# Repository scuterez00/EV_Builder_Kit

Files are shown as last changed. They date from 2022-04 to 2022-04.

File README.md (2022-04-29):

# EV_Builder_Kit Engineering Addendum
Erbyn Bonilla, Henry Chong, Stephanie Cuterez, Linglong Le, Michelle Imogu

EC464 - Spring 2022

## Summary and Project Motivation
As countries and institutions start pushing to replace fossil fuel driven vehicles with zero emission vehicles such as electric cars, there will inevitably be skepticism and doubt expressed towards this change. These doubts have a variety of sources, whether it be a lack of familiarity with how electric vehicles work, or a belief that electric vehicles cannot operate as well as gas powered vehicles. To combat these sources of doubt, this project will create a small-scale model of a transportation grid completely powered by electric vehicles. There will be multiple small vehicles that users can drive around and link with provided charging stations for recharging. These vehicles will transmit mileage and battery charge remaining in the model car to the users. A set of controllers will also be provided for user interaction with the model, allowing people to come up and drive the vehicles around.  Charging stations utilizing a variety of methods, ranging from solar panels to outlet power, will be provided for recharging the vehicles. And everything will be integrated into a set of roads and decorations to create a semi-realistic transportation system. This will create an electric vehicle kit that will show the operation cycle of electric vehicles. In the process of using the kit, users will be provided with a clear demonstration of the process of charging, driving, and recharging the vehicles. 

## Main Features of this Repository
As of now, the repository contains all the schematics needed for the replication of the casing and circuitry of two items: the electric vehicles and the controllers for these electric vehicles. Associated datasheets and schematics for this portion of the project can be accessed using [README_HARDWARE.md](README_HARDWARE.md). Additionally, this repository also contains the code that must be uploaded to the microcontrollers on the cars and controllers for the communications between the two to begin. For a brief summary of the code please view [README_SOFTWARE.md](README_SOFTWARE.md).

## Current State of the Project
### Cars
The information in this repo corresponds to a set of working electric vehicles that can drive forwards, backwards, and turn in response to a users inputs on an associated controller. The car is capable of sending relevant battery data to the controller via the transceiver, and displays the current state of control using LEDs. When the power is switched off the car is still capable of charging via a DC jack connected to either a solar panel or a DC adapter, or a USB-C cable.

The method the cars use to drive around is via differential drive, meaning that the two back wheels can rotate independently of each other, while the front wheels are left to be free spinning. This was done to reduce the amount of motor drivers required as compared to four wheel drive, and reduce the complexity of the mechanical system required to create front wheels for facilitating turning.

One thing to note is that no PCB was utilized for any of the electronics, and as a result there are no PCB files available for creating the circuitry outlined in the hardware report. Similarly no CAD was utilized for the creation of the car bodies, so no files are available for quickly reproducing the bodies via machining.

### Controllers
The information in this repo corresponds to a working controller that can communicate with the cars, and display relevant details about the car onto the attached LCD. Using the joysticks, the user will be able to control the vehicle, while the toggle switches are used to switch which vehicle is being controlled. The controller provided here uses 3 switches to toggle between 3 possible cars for control. The controller is powered using 4 AA batteries, and as a result requires new batteries to be provided upon running out of charge.

The current set-up of the controller is so that the left joystick is pushed vertically to control the car's forward/reverse motion, while the right joystick is pushed horizontally to cause the car to turn. To know which car the controller is controlling, flip the switches to toggle between vehicles, and look for the vehicle with a lit up LED. The LED corresponds to having an open reading pipeline to receive controller data.

### Track and Surrounding Model
Tracks and auxiliary models such as grass, trees and buildings were also used in the project, but have not been included in this repository. This is because the models were purchased and not designed, thus their CAD files and designs cannot be placed into this repository. As for the track, this track simply consists of adhesive black tape laid out onto flat boards to denote roadway, and as a result not included in this repository either.

## Things to look out for
- Depending on the type of microcontroller you are using, specific drivers will be required. In our case we were not using official Arduino Nano microcontrollers for our project, thus we had to use the CH340 drivers. If you are using official microcontrollers these drivers will not be needed.
- The nRF24L01 transceivers have only a single pipeline for communication, which means that they cannot transmit and receive at the same time. To circumvent this our code uses cycles to switch between transmission and reception mode on the transceivers of the controllers and the cars. The controller's transceiver first sends out a specific message while swapping to receiving. This message will cause the transceiver on the car to close the pipeline, and then switch from receiving to transmitting, before transmitting a message. Once the controller transceiver receives this message, they send out another signal which will return the controller's transceiver to transmission mode and the car's transceiver to reception mode.
- Due to the use of differential drive, the center of gravity of the the vehicle, along with the traction of the wheels are critical for the cars to handle properly. This means that the center of gravity should be shifted towards the central axis of the differnetial drive.

## Known Bugs
- Occasionally the cars will become completely unresponsive to the controller, and switching the power button will not be able to solve this. To fix this issue unplug the battery from the car, then flip the power switch 5 times. After this you can replug the battery and the system should work again.

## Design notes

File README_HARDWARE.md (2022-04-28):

# Hardware Report
This is a report which covers the fundamentals of the hardware, including both the circuitry and the casing/bodies made to house the products.

## Cars
This section will deal with the circuitry and casing for the electric cars.

### Car Bodies
**Car Front:**
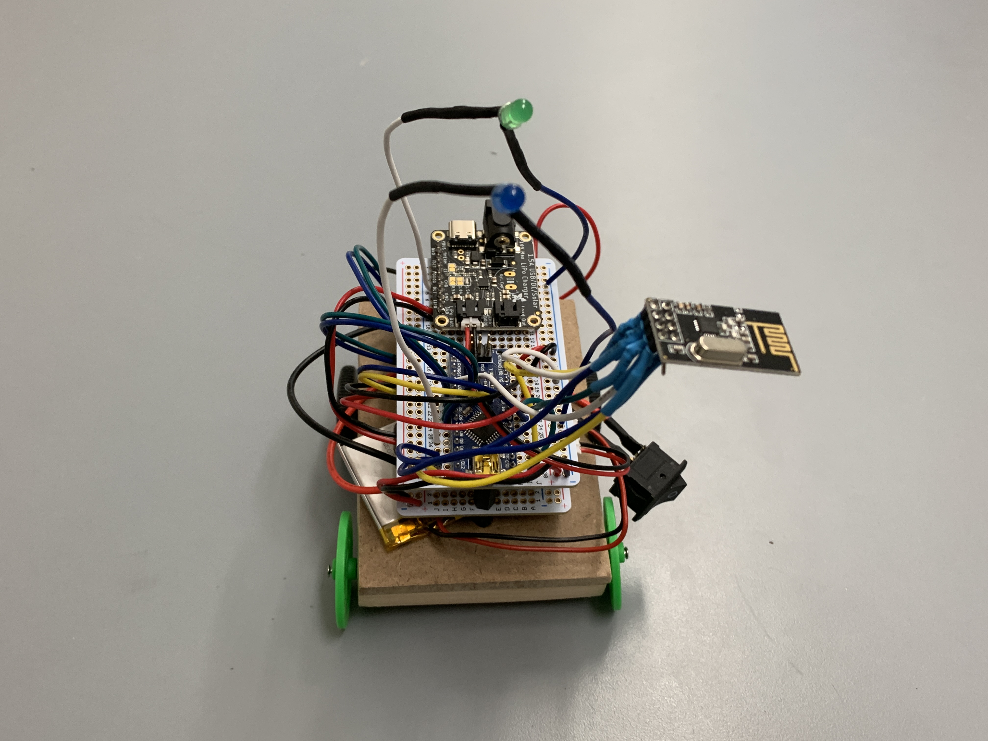
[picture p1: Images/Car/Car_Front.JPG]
Car Front


**Car Side:**
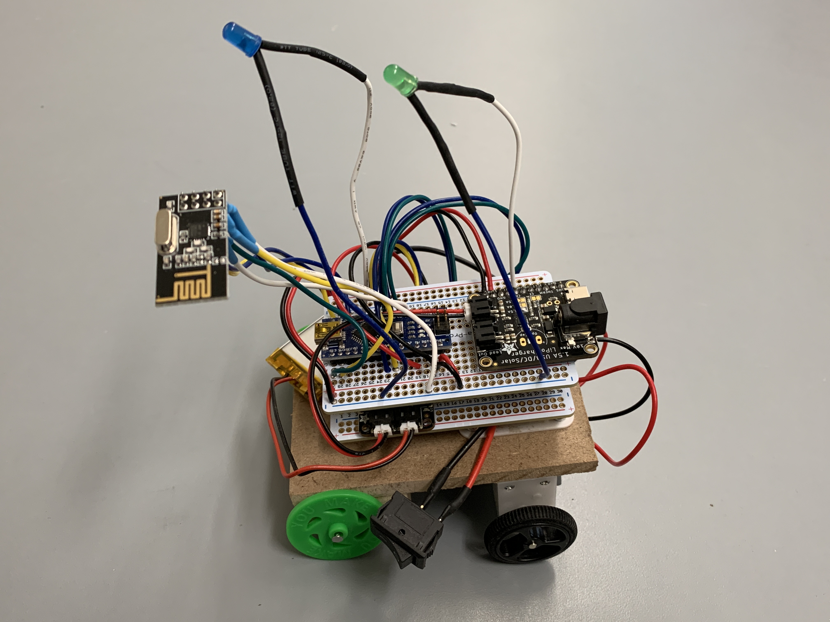
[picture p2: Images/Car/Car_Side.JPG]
Car Side


**Car Back:**
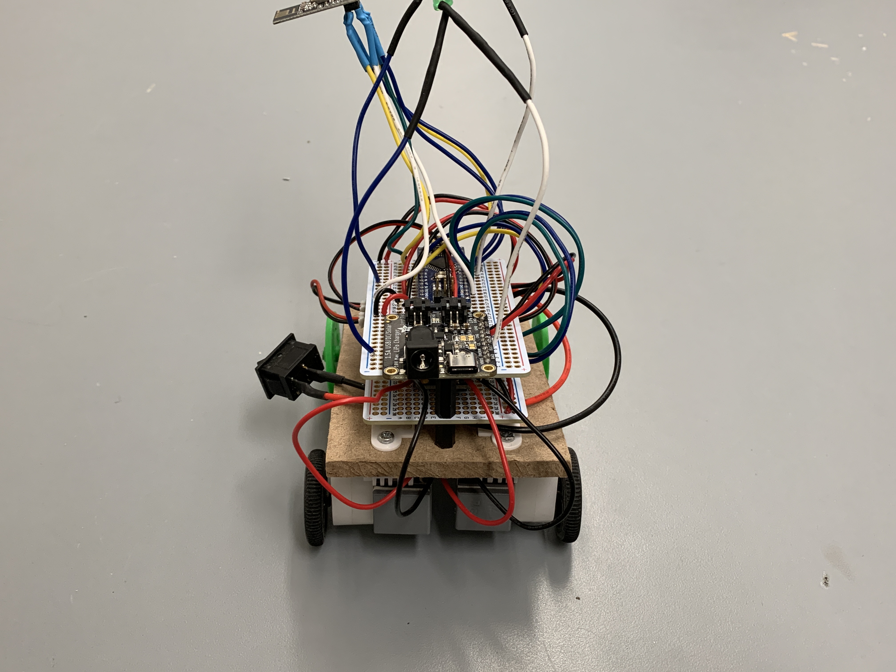
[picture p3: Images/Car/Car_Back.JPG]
Car Back


**Car Bottom:**
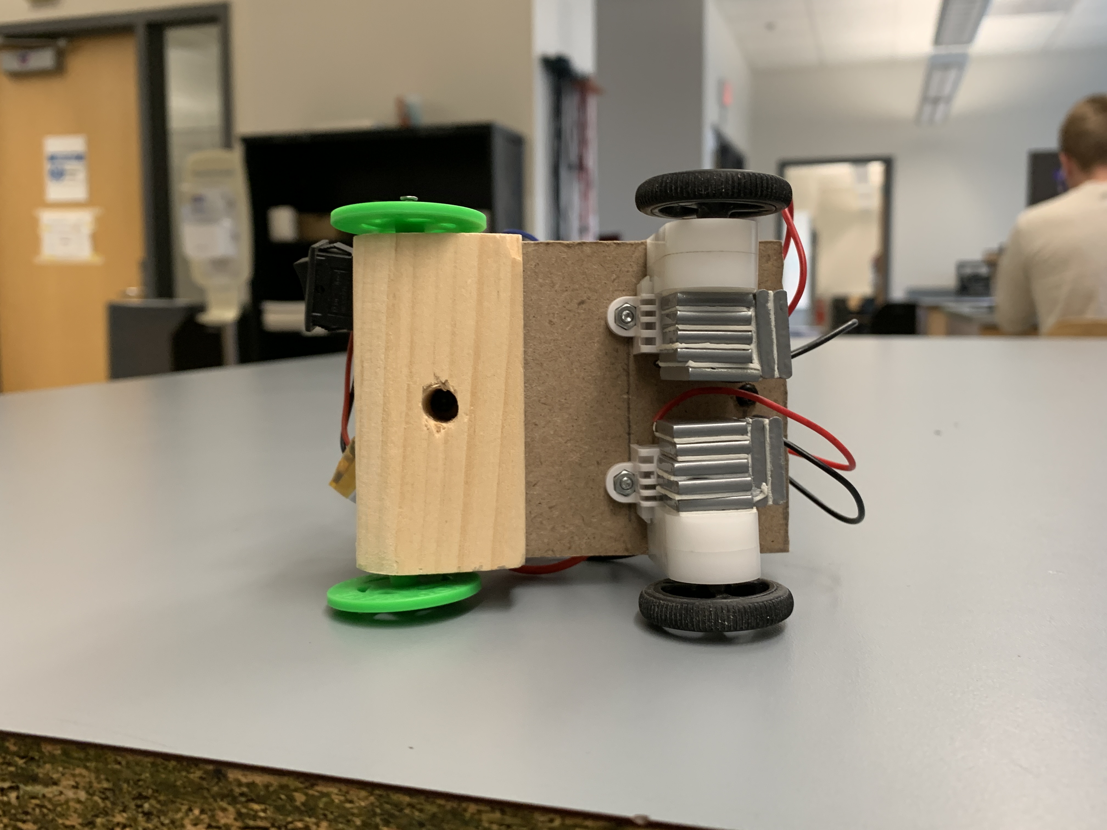
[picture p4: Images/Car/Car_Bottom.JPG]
Car Bottom

  Shown here are 4 views of one of the fully assembled cars. The car in question here is a Light Duty Vehicle(LDV) Equivalent. The car body was made using 1/8" thick Medium-Density Fiberboard(MDF) and 2" by 1" wood planks. The MDF board is used to house the circuit tower and mount the motors and weight, while the wood plank is used to hold the front wheels in place, using nails. Holes were drilled into the MDF board for the purpose of screwing in the circuitry components. A large hole was drilled into the bottom of the 2" by 1" plank so that screws could be attached to hold the entire circuit tower in place.

### Car Circuitry
**Circuit Tower Bottom:**
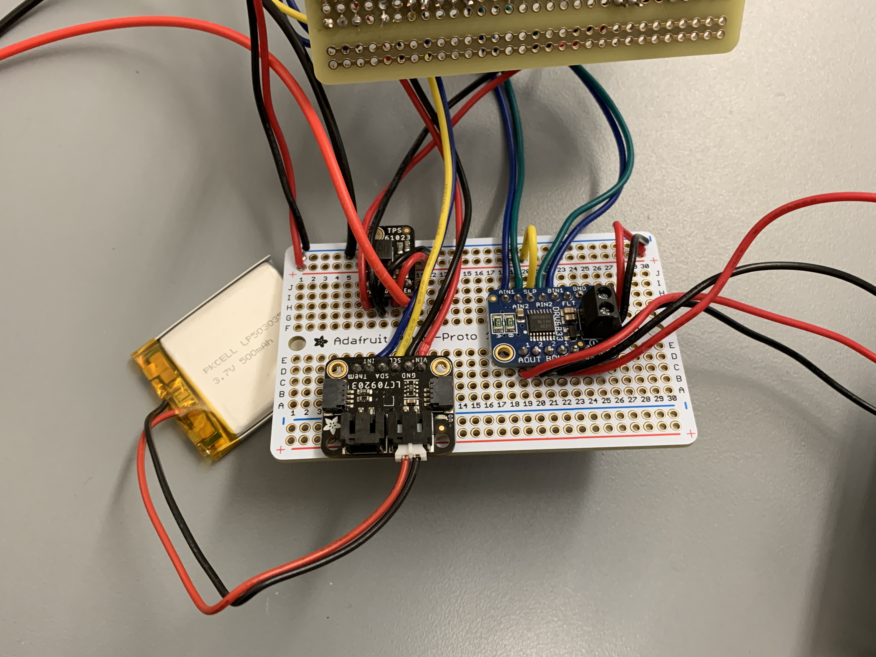
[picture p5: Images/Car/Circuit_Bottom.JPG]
Circuit Tower Bottom

  The circuitry from the car is soldered onto two breadboards, and mounted one on top of the other using PCB screws. The picture above shows three major components: the motor driver, the battery monitoring chip, and the voltage regulator. The motor driver is responsible for controlling motor speed and direction, while the battery monitoring chip provides data on the battery charge and state. The voltage regulator is used to convert the 3.7 Volts from the lithium polymer(LiPo) battery to 5 Volts for the rest of the system. One thing to note is that the on-off switch attached to the vehicle is linked to the Enable(EN) pin of the voltage regulator. When the switch is turned off the EN pin is pulled to ground, disabling the 5 Volt output powering the car circuitry, while keeping the battery connected to the charging circuit.

**Circuit Tower Top:**
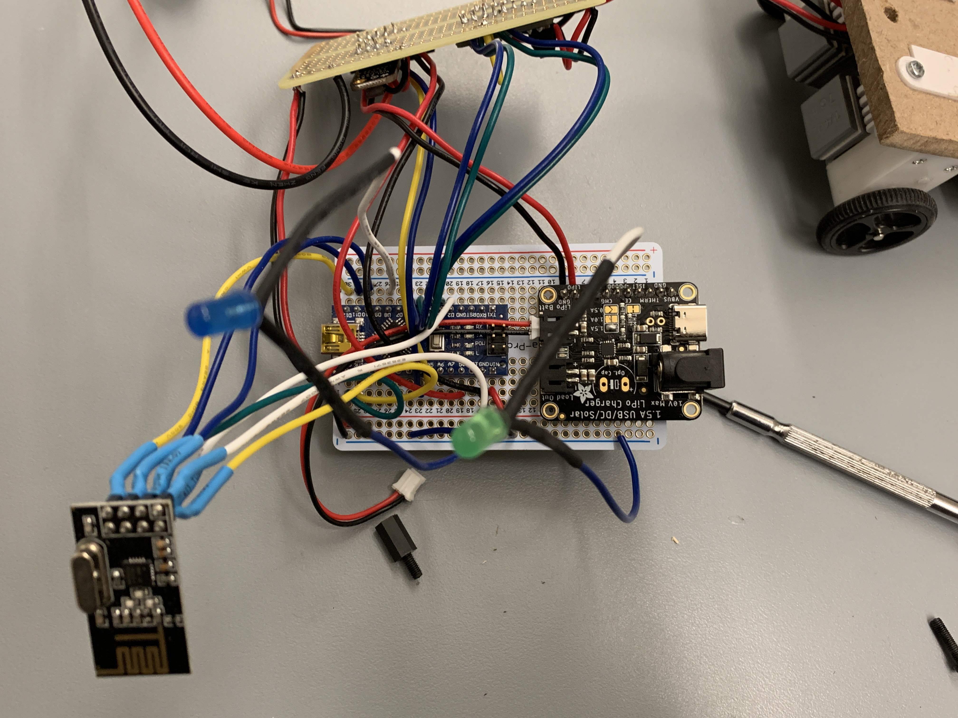
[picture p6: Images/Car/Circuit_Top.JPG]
Circuit Tower Top

  Shown here is the top of the circuitry tower, which contains the following: the NRF24L01 transceiver chip, the microcontroller (an Elegoo Nano), and the LiPo Charging chip. The transceiver is responsible for communication between the car and the controllers, while the microcontroller is responsible for performing all the computations and translations necessary to control each component of the car. The LiPo Charging chip is attached to provide a regulated method of charging the LiPo battery, utilizing either a 3.5 mm DC jack, or a USB type C Cable. Also shown here are LEDs attached to provide the user feedback on control and charging.

### Car Circuit Schematic

[Link to PDF](/Circuit_Schematics/Car_Circuit_Abstraction.pdf)

[Link to PDF](/Circuit_Schematics/Car_Circuit.pdf)
 
Shown here is a circuit diagram and an associated abstraction. Essentially the circuit can be split up into two different components, the battery circuit and the operational circuit. The operational circuit operates on 5 volts and consists of: the microcontroller, voltage regulator, motor driver, motors, and transceiver. This circuit is what drives radio communication and driving of the car. The battery circuit on the other hand consists of the LiPo Fuel Gauge and the LiPo Charging Chip, and serves to monitor and recharge the battery. The output of the battery circuit is fed to the voltage regulator to actually power the rest of the operational circuit. Thus by turning off the voltage regulator using a switch, we are able to maintain the ability to charge the battery while cutting power off from the car.

### Car Body Schematic

[Link to PDF](/Hardware_Schematics/Car_Schematic.pdf)

Shown here is the drawing used to create the body of the cars. This is the drawing for the LDV variant of the cars. The body is made up of two main components: the 1/8" thick MDF board and the 2" by 1" wood plank. The MDF board is drilled so that all the circuit components can be attached using screws, while the plank is super glued to the front of the MDF board, for mounting the wheels. Once all the circuitry has been attached and screwed in, steel weights are then added to the back of the vehicle, to improve the vehicle's handling by shifting the center of gravity towards the motored wheels. No CAD files were created as all components were made by hand.

### Bill of Materials
#### Light Duty Vehicle(LDV) variant Car

This bill of materials covers the material needed to create one LDV car, and does not include components such as nails, screws and wires.

| Item | Amount | Vendor | Datasheet Link |
| --- | :---: | :---: |:---: |
| Microcontroller | 1 | Amazon | [Link](/Data_Sheets/Nano_Pinouts.pdf)|
| Transciever | 1 | Amazon | [Link](/Data_Sheets/nRF24L01_Datasheet.pdf)|
| Battery Monitoring Chip| 1 | Adafruit  | [Link](/Data_Sheets/Battery_Monitor_Datasheet.pdf)|
| Battery Charging Chip | 1 | Adafruit | [Link](/Data_Sheets/Charger_Datasheet.pdf)|
| Battery | 1 | Adafruit |  [Link](/Data_Sheets/Battery_Datasheet.pdf)|
| Voltage Regulator| 1 | Pololu |  [Link](/Data_Sheets/Pololu_Regulator_Sheets/Chip_Datasheet.pdf)| 
| Motor Controller | 1 | Adafruit | [Link](/Data_Sheets/Motor_Driver_Datasheet.pdf)| 
| Plastic Motor | 2 | Pololu | [Link](/Data_Sheets/Plastic_Motor_Specifications.pdf)|  
| Motor Wheels | 2| Pololu | [Link](/Data_Sheets/Dimensions/Pololu_Wheel_Dimensions.pdf)|
| Plastic Motor Brackets | 2 | Pololu | [Link](/Data_Sheets/Dimensions/Plastic_Motor_Mounts_Dimensions.pdf) |
| Front Wheels | 2 | Amazon | [Link](https://www.amazon.com/gp/product/B073W18BP3) |
| Steel Weights | 10 | Amazon | [Link](https://www.amazon.com/gp/product/B06XDHXRT7)|
| Solderable Breadboard | 2 | Adafruit | [Link](https://www.adafruit.com/product/1609)|
| LEDs | 2 | Amazon | N/A |
| 1/8" MDF Board| 1 | Home Depot | N/A |
| 2" by 1" Plank | 1 | Home Depot | N/A |

#### Heavy Duty Vehicle(HDV) variant Car

This bill of materials covers the material needed to create one HDV car, and does not include components such as nails, screws and wires.

| Item | Amount | Vendor | Datasheet Link |
| --- | :---: | :---: |:---: |
| Microcontroller | 1 | Amazon | [Link](/Data_Sheets/Nano_Pinouts.pdf)|
| Transciever | 1 | Amazon | [Link](/Data_Sheets/nRF24L01_Datasheet.pdf)|
| Battery Monitoring Chip| 1 | Adafruit  | [Link](/Data_Sheets/Battery_Monitor_Datasheet.pdf)|
| Battery Charging Chip | 1 | Adafruit | [Link](/Data_Sheets/Charger_Datasheet.pdf)|
| Battery | 1 | Adafruit |  [Link](/Data_Sheets/Battery_Datasheet.pdf)|
| Voltage Regulator| 1 | Pololu |  [Link](/Data_Sheets/Pololu_Regulator_Sheets/Chip_Datasheet.pdf)| 
| Motor Controller | 1 | Adafruit | [Link](/Data_Sheets/Motor_Driver_Datasheet.pdf)| 
| Metal Motor | 2 | Pololu | [Link](/Data_Sheets/Metal_Motor_Datasheet.pdf)|  
| Motor Wheels | 2| Pololu | [Link](/Data_Sheets/Dimensions/Pololu_Wheel_Dimensions.pdf)|
| Metal Motor Brackets | 2 | Pololu | [Link](/Data_Sheets/Dimensions/Metal_Motor_Mount_Dimensions.jpg) |
| Front Wheels | 2 | Amazon | [Link](https://www.amazon.com/gp/product/B073W18BP3) |
| Steel Weights | 30 | Amazon | [Link](https://www.amazon.com/gp/product/B06XDHXRT7)|
| Solderable Breadboard | 2 | Adafruit | [Link](https://www.adafruit.com/product/1609)|
| LEDs | 2 | Amazon | N/A |
| 1/8" MDF Board| 1 | Home Depot | N/A |
| 2" by 1" Plank | 1 | Home Depot | N/A |

## Controllers
This section will deal with the circuitry and casing for the controllers.

### Assembled Controller

**Controller Top:**
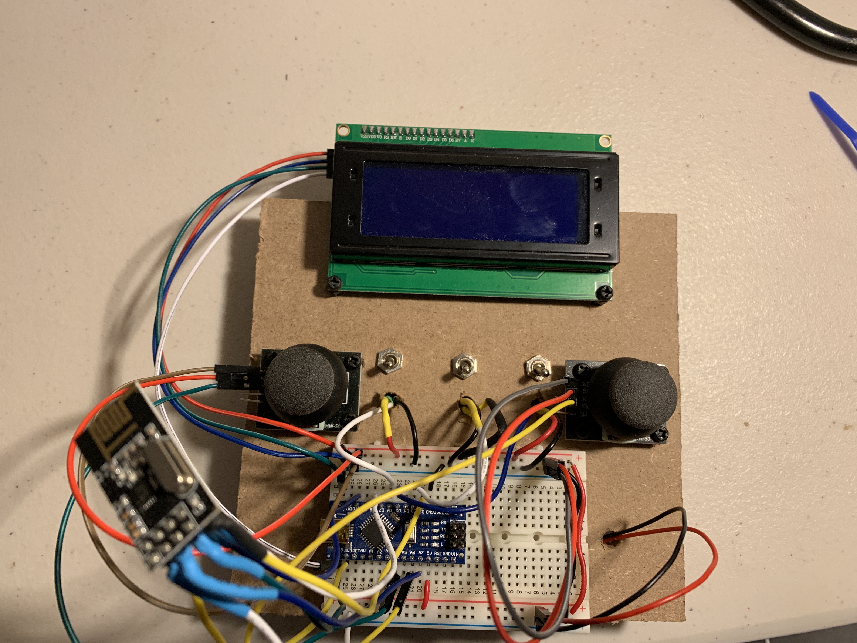
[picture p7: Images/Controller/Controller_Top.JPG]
Controller Top

**Controller Side:**
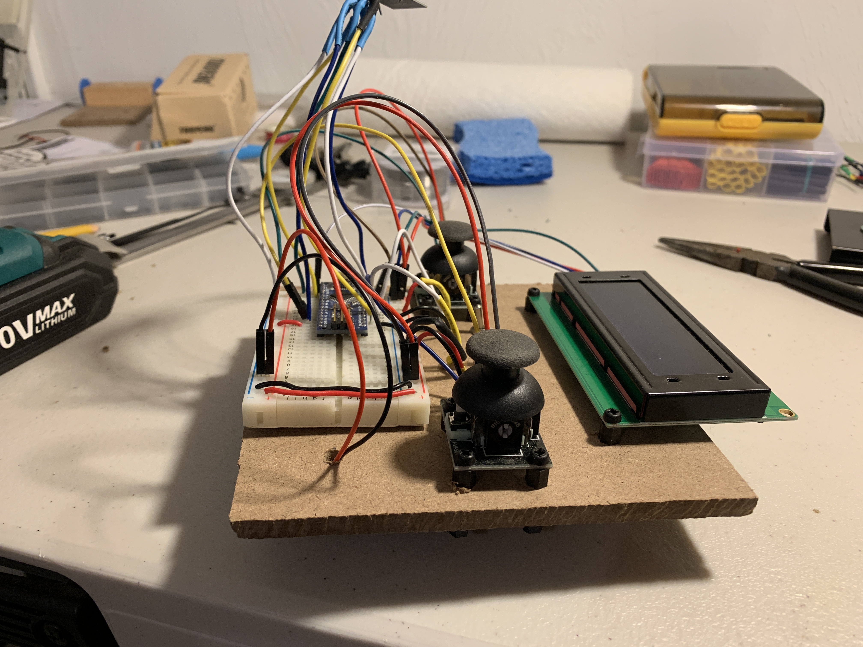
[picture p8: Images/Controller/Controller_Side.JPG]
Controller Side

**Controller Bottom:**
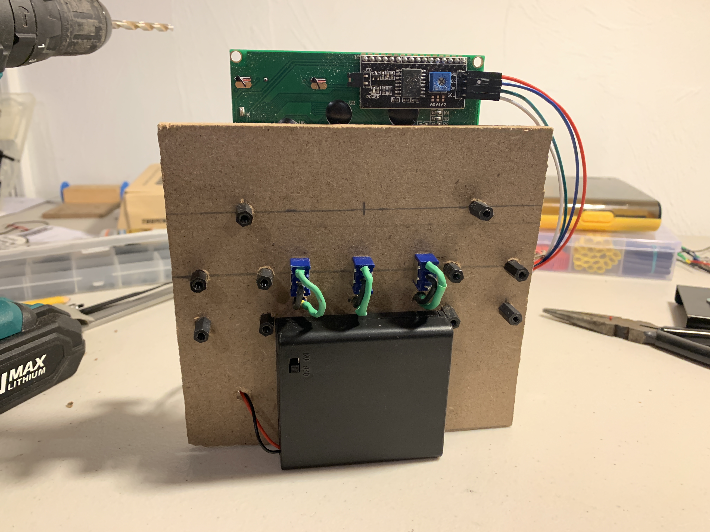
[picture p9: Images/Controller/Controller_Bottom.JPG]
Controller Bottom

**Controller Held:**
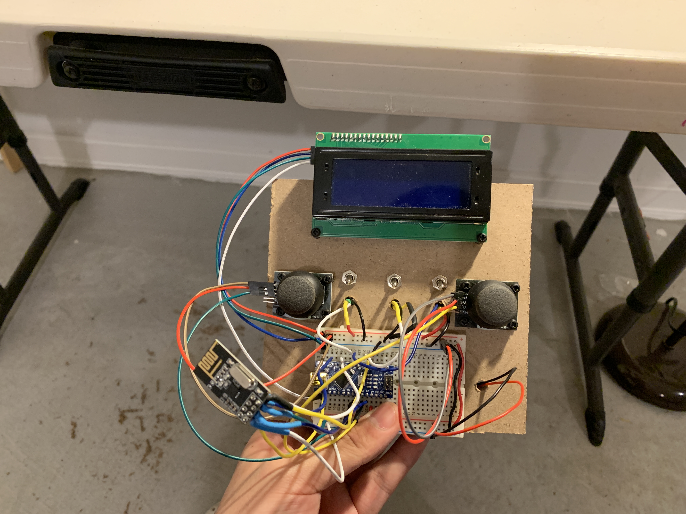
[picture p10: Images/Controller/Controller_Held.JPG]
Controller Held


  Shown here are 4 views of one of the fully assembled controller. The controller body was made using 1/8" thick Medium-Density Fiberboard(MDF). Holes were drilled into the MDF board for the purpose of screwing in the joysticks, LCD, and toggle switches. Additional holes were also made for the purpose of routing wire from the bottom of the controller to the top, which has the breadboard attached. On the breadboard itself is simply a microcontroller and an attached NRF24l01 transciever. Taped to the back is the battery pack, which can be switched on or off to provide power to the controller.
  On the controller there are three toggle switches in the center, and LCD, and two joysticks. The joysticks are responsible for taking user input and converting that into motion on the cars. The left joystick is pushed forward/back to control the cars forward or reversing speed, while the right joystick is pushed horizontally to turn the car. The toggle switches are used to switch between cars, as each controller is capable of communicating with up to 3 cars. And the LCD is responsible for displaying the battery life and mileage remaining on each of the cars.
  
### Controller Circuit Schematic

[Link to PDF](/Circuit_Schematics/Controller_Circuit_Abstraction.pdf)

[Link to PDF](/Circuit_Schematics/Controller_Circuit.pdf)

As shown in the circuit diagram and abstraction, the controller circuit is only one circuit, which uses the microcontroller as the central hub. The battery pack routes power to the microcontroller, which then takes inputs from the various switches and joysticks on the controller. Once the inputs have been received, the microcontroller translates them into packets to be sent via the transceiver. However the transceiver also receives packets and sends these packets to the microcontroller, which then translates these packets into information, and displays this information onto the LCD.

### Controller Body Schematic

[Link to PDF](/Hardware_Schematics/Controller_Schematic.pdf)

This details the size of holes, and location of holes required to be drilled into a 1/8" thick MDF board for all the components to be properly screwed in. No CAD Files were created as all components were made by hand. 

### Bill of Materials

This bill of materials covers the material needed to create one controller, and does not include components such as nails, screws and wires.

| Item | Amount | Vendor | Datasheet Link |
| --- | :---: | :---: |:---: |
| Microcontroller | 1 | Amazon | [Link](/Data_Sheets/Nano_Pinouts.pdf)|
| Transciever | 1 | Amazon | [Link](/Data_Sheets/nRF24L01_Datasheet.pdf)|
| Breadboard | 1 | Adafruit | [Link](https://www.adafruit.com/product/4539)|
| Battery Pack | 1 | Adafruit |  [Link](/Data_Sheets/Battery_Pack_Datasheet.pdf)|
| Joystick | 2 | Amazon | [Link](https://www.amazon.com/ARCELI-Joystick-Controller-Dual-axis-Breakout/dp/B077Z8QN3S)| 
| Toggle Switch | 3 | Amazon | [Link](https://www.amazon.com/Gikfun-MTS102-Position-Toggle-Arduino/dp/B01BWL7Z44)|  
| LCD Display | 1 | Amazon | [Link](https://www.amazon.com/gp/product/B01GPUMP9C)|
| AA Batteries | 4 | Adafruit |  N/A | 
| 1/8" MDF Board| 1 | Home Depot | N/A |

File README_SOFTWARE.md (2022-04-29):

# Software Report
This report discusses the code used for both the vehicles and controllers for the project.

## Software Used
Used in: Arduino 1.8.16
The coding for the project has two main files which are all used through an Arduino. The two file codes are the controller file which is the transmitter.ino and the vehicle file which is the receiver.ino.

## TRANSMITTER.ino
The transmitter.ino file contains all the code for the controller to be able to control the cars per the user inputs. The only library that is needed to be installed for the code to work is LiquidCrystal_I2C. This library can be installed from https://github.com/fdebrabander/Arduino-LiquidCrystal-I2C-library.  This makes it so the model attached to the LCD is converted from multiple pins to only 4 pins needed to connect to the controller. Important note for power is for a wireless controller, a power supply is given. The power supply needs to be connected to the Vin pin with the red wire and GND pin with the black wire. The transmitter code will have a block of switch cases that detect which switches are toggled. There are a total of 3 toggle switches where each one controls a specific car by having a unique 6-bit address. Within the switch cases, there is a code running that will decrease the miles of the choosen vehicle. Once the miles reaches zero, it will go into a if statement where it will print on the LCD a 'needs charging' label. This will make it so that the specific switch case will be stuck in a while loop and prevent any additional 3-bit message to be sent which in turn prevents the vehicle from moving. Only when the user truns off the specific switch on another will it then go out of the loop.

### (Joysticks Section)
The left joystick code only reads the y position of the joystick, which then reads the position. Anything above the position of 500 will be considered a forward input to the vehicle and anything less than 500 will be considered backwards input. There are 7 possible positions that the joysticks can register with each one sending a 3-bit message which includes moving forward, backwards, left, right, different speeds, or not move at all. All of these messages are attached to the coordinate positions of the joysticks.

### (switch_to_receiver function)
The function will first send a 3-bit message to the receiver to let it know to switch from reading to writing. After, the trasmitter will switch the radio from writing to reading. It will wait a couple of cycles with the while loop until it detects that a radio channel is available. Once the radio channel is available, it will obtain a string of the battery level, which then will be converted to a float. The float will be displayed on the LCD so that the user can see it.

### (LCD)
The first thing that is needed is to set the pins that will be used to setup the LCD are Vdd, GND, and two pins on the board to print onto the LCD. The function needed to use the LCD is LiguidCrystal_I2C which will set up the LCD. During the setup block, the LCD prints the name of vehicle that we EV are imitating and labeling miles and battery. During the loop block, the LCD will print battery and milage of the choosen vehicle every so often.

## RECEIVER.ino
The receiver.ino file contains all the code for the vehicle to read the inputs of the controller and adjust the motors. The libraries that must be installed for the code to work are: Adafruit's LC709203F library, and the nRF24L01 libraries. The LC709203F library is required for the I2C communication of battery data from the connected chip to the microcontroller, while the nRF24L01 libraries are necessary for the transceiver. No additional files are needed for the code to work successfully. The Arduino code can be uploaded directly to an Arduino Nano and should work properly. The code will always go through a while loop when the radio is available in that channel. If available, the code will obtain a 3-bit message sent from the controller and go through if statements to see which message was detected. There are 8 available 3-bit messages to send. 7 of those messages are to determine the action of the motors which includes moving forward, backwards, left, right, adjusting speeds, or to not move at all. In addition there is a single line of code where and LED will turn on if the radio is available so that the user has a visual representation of what vehicle they are using.

### (transmitter function)
The transmitter function will activate once the receiver obtains the 3-bit message to switch from reading to writing. If this is shown, it will go into the if statement and convert the float battery percentage to a string so that it can be sent through the transmitter. Once it sends the message, the transmitter will then switch from writing to reading so that it can obtain more 3-bit messages.

## Drivers Required
In the case that you are not using official Arduino Microcontrollers for this project, then it will be necessary to install certain drivers for the code to upload properly. In most cases this will be the CH340 drivers.

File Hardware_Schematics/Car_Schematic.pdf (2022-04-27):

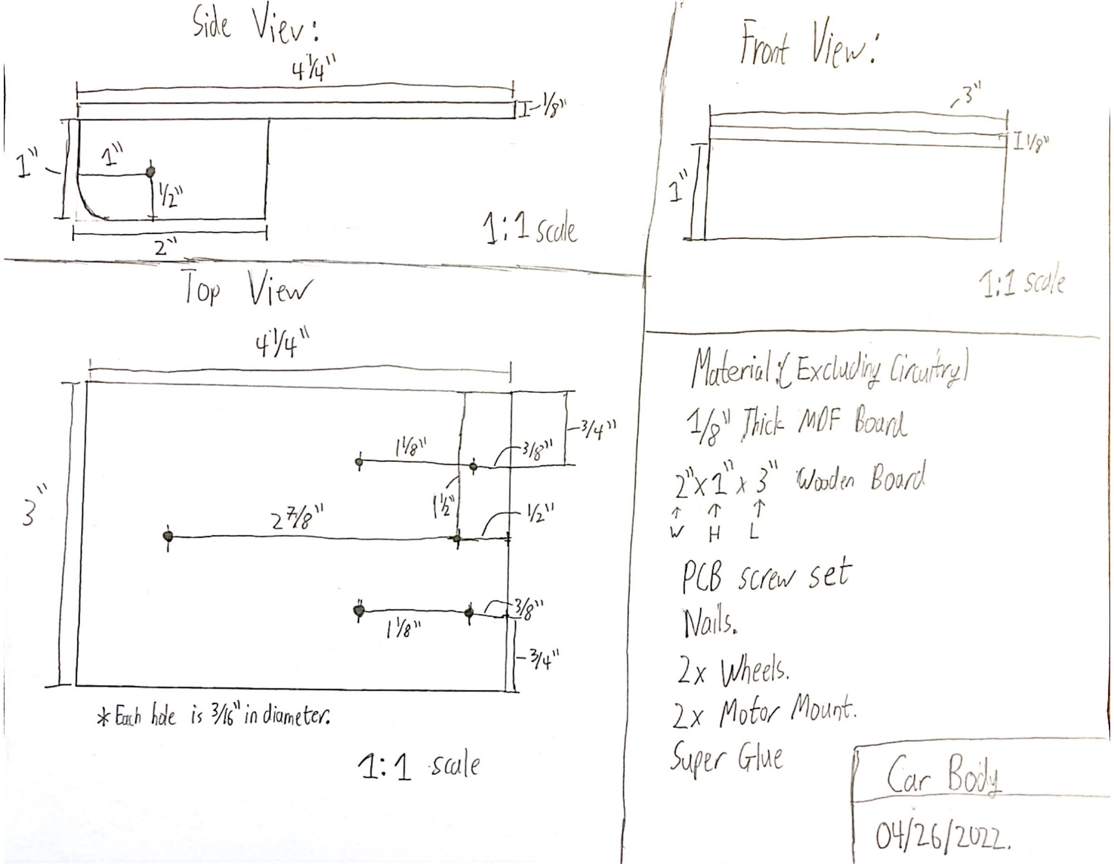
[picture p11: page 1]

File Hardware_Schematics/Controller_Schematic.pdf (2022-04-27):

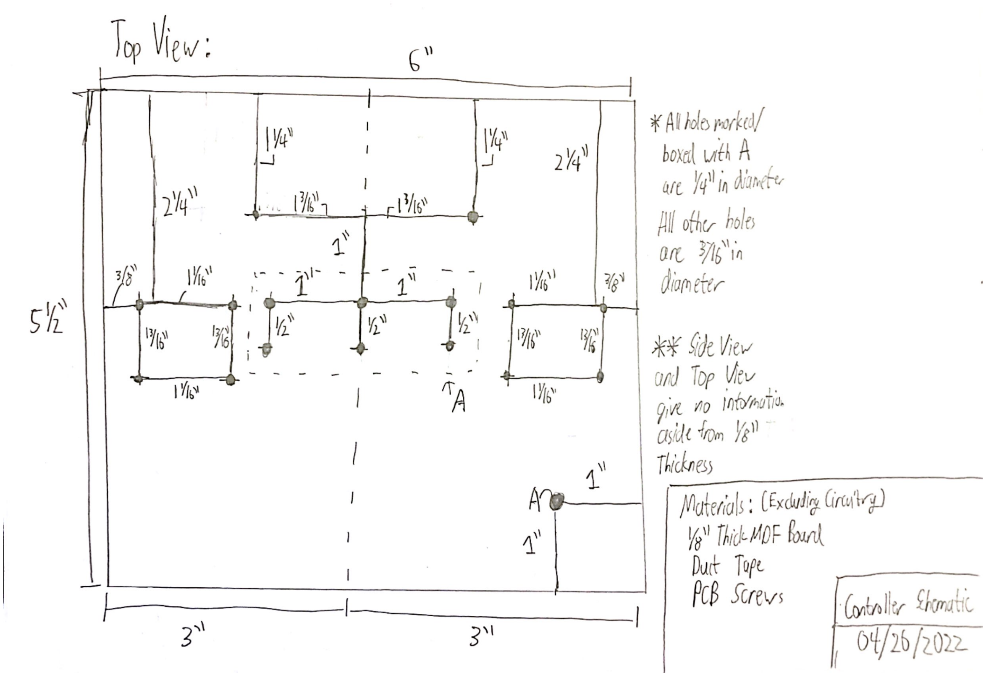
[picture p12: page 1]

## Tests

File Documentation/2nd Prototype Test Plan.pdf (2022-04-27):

# Memo

To: | Professor Pisano
From: | EV Builder Kit Team
Team: | 18
Date: | 03/01/22
Subject: | Prototype Testing Plan

# Table of Contents

1.0 Required Materials | Pg 2
1.1) Car Materials
1.2) Controller Materials
1.3) Charging Station Materials

## 2.0 Testing Setup and Explanation Pg 4

2.1) Introduction
2.2) Car Testing Setup
2.3) Controller Testing Setup
2.4) Charging Station Testing Setup
3.0 Testing Procedure - | Pg 6
3.1) Car Testing Procedure
3.2) Controller Testing Procedure
3.3) Charging Station Testing Procedure
4.0 Measurable Criteria | Pg 7
4.1) Car Testing Criteria
4.2) Controller Testing Criteria
4.3) Charging Station Criteria

## 5.0 Scoring Sheet & Appendix Pg 8

5.1) Car Scoring Sheet
5.2) Controller Scoring Sheet
5.3) Charging Station Scoring Sheet

## 1.0 Required Materials

### 1.1 Car Materials

Hardware Materials for Car 1
- Full Breadboard (1)
- Arduino Nano (1)
- 3.7 Volt 500 mAH Lithium Polymer Battery (1)
- Dual H-Bridge Motor Controller (1)
- NRF24L01 Transceiver Chip (1)
- Adafruit LC709203F LiPoly Fuel Gauge (1)
- 5-Volt Voltage Booster Chip (1)
- N20 DC Motors and Mounts (2)
- Lego Cross Wheels (2)
- Standard Plastic 40mm Wheels (2)
- Wood Plank (1)
- LCD Display
- 22 AWG Wire of Assorted Colors
- Heat Shrink Tubing
Hardware Materials for Car 2
- Proto Breadboard (2)
- Elegoo Nano (1)
- 3.7 Volt 500mAH Lithium Polymer Battery (1)
- Dual H-Bridge Motor Controller (1)
- NRF24L01 Transceiver Chip (1)
- Adafruit LC709203F LiPoly Fuel Gauge (1)
- 5-Volt Voltage Booster Chip (1)
- Pololu Plastic Motors and Mount(2)
- Pololu 32mm Plastic Wheels (2)
- Standard Plastic 40mm Wheels (2)
- MDF Board (1)
- 22 AWG Wire of Assorted Colors
Software Materials
- Arduino Script
- Cycle through various motor states to autonomously drive forward, backward, and turn left and right.
- Read inputs from the fuel gauge chip, and send data via transceiver to display on the controller.

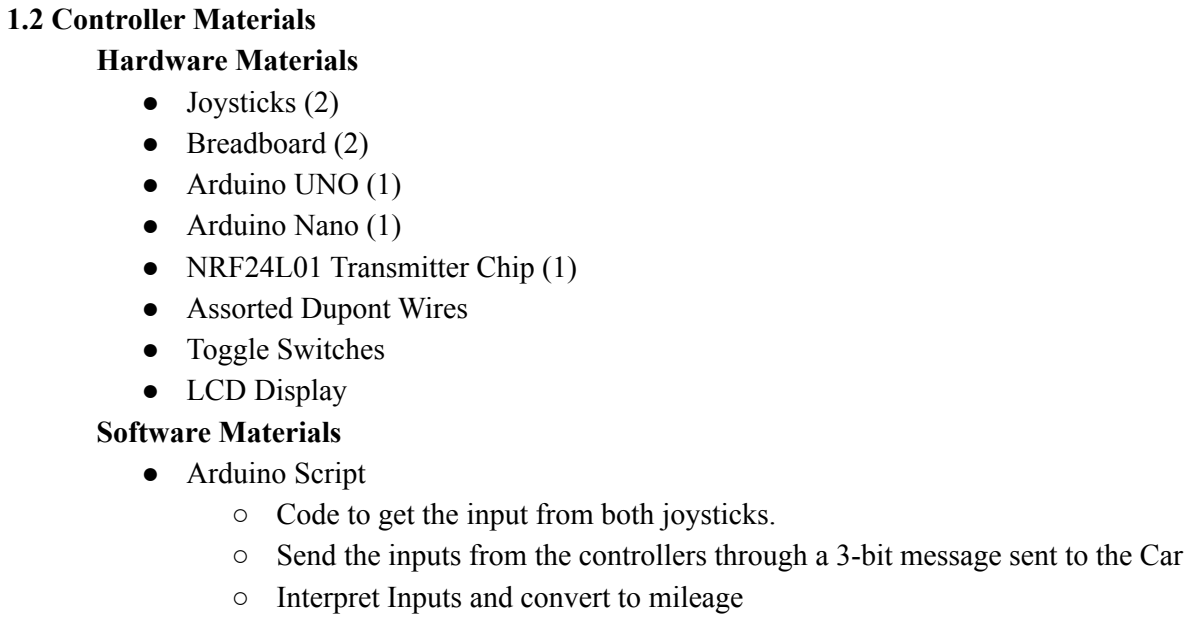
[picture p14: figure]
1.2 Controller Materials Hardware Materials ● Joysticks (2) ● Breadboard (2) ● Arduino UNO (1) ● Arduino Nano (1) ● NRF24L01 Transmitter Chip (1) ● Assorted Dupont Wires ● Toggle Switches ● LCD Display Software Materials ● Arduino Script

- Code to get the input from both joysticks.
- Send the inputs from the controllers through a 3-bit message sent to the Car
- Interpret Inputs and convert to mileage

### 1.3 Charging Station Materials

Hardware Materials
- Cardboard Stand (1)
- 6V 2W Solar Panel (1)
- 5.5’Aluminum Reflector Lamp (1)
- 9W Hydroponic Bulb (1)
- Wood Light Stand (1)
- Li-Po Battery Charging Circuit Chip (1)
- 3.7 Volt Lithium Polymer (LiPo) Battery (1)
- Digital Multimeter (1)
- Industrial cardboards

## 2.0 Testing Setup and Explanation

### 2.1 Introduction

The tests can be split up into three categories: testing the cars, testing the controllers, and testing the charging station. The cars act as the main body of interest for all three of these tests, as they are set up with motors, transceivers, and a battery. This allows the car to interact with the charging station and controller, and produce visible outputs from the test directly.

Car:
On each car, there is a 3.7 volt lithium polymer(LiPo) battery which is used to power the vehicle. This battery is attached to a LiPo fuel gauge chip, which is able to take in a LiPo Battery connection. The fuel gauge chip has output pins which are fed directly to the Arduino Nano, as well as into a 5-Volt Voltage Booster. The direct feed to the Arduino Nano is for the purpose of measuring battery state, sending that data to the transceiver, so that it can be displayed properly on the Controller’s LCD display. The 5-Volt voltage booster raises the 3.7 volt output from the battery to a 5 volt output, and feeds that voltage to power the Arduino Nano and dual H-Bridge motor controller. The motor controller is connected to two DC motors, while the Arduino Nano is connected to the motor controller. The Nano can then control the motors by applying Pulse Width Modulation(PWM) and shifting between logic high to logic low on the connections to the motor controller. A transceiver module is also attached to the Nano, allowing an external controller to control the signals sent to the motor controller, and thus the motors from there.
Note: For this prototype the LCDs are not on the controller, as we ran into a little issue with transmitting and receiving at the same time. So one car will have an LCD attached to display battery state

Controller:
On the controller, there are 2 axial joysticks, which are connected to an Arduino Uno. The uno is able to take in the inputs from these joysticks, and use an attached transceiver chip to transmit an 3 bit message to the transceiver on the car. This allows the car to read the 3 bit message from the controller, and adjust its state accordingly. Furthermore, the controller will have a toggle switch you use to switch between which car you want to control.

Charging Station:
For the charging station, an aluminum lamp with a hydroponic bulb is used. This is as the hydroponic bulb mimics the visible light spectrum that would be expected from the sun, which is where most of the energy from the solar panels are derived. This lamp will be directed towards a solar panel, which is connected to a Lithium Polymer Charging Chip. This chip is capable of using the power from the solar panel to recharge the battery, while also load balancing to the output as well. For this prototype, the main proof of concept is to show that using a lamp to power the solar panel is viable.

### 2.2 Car Pre-Testing Setup

1. Connect the Arduino Nano to a computer with the autonomous code loaded onto it
2. Upload the code from the computer to the Arduino Nano
3. Disconnect the computer from the Arduino Nano
4. Clear out an area on the ground for the car to operate on
5. Repeat steps 1-4 with the car that is operating using the Elegoo Nano.

### 2.3 Controller Pre-Testing Setup

1. Connect the Arduino Nano on the car to computer
2. Upload the code onto the Arduino Nano
3. Disconnect the Nano and place the car on ground
4. Connect the Controllers Arduino Uno to the computer for power.
5. Upload the code onto the Arduino Uno

### 2.4 Charging Station Pre-Testing Setup

1. Solar lamp is stored in the kit for portable use
2. Take the solar lamp out and clamp it on the side of the kit
3. The kit wall is able to hold the weight of the lamp
4. Turn the lamp towards the solar panel, and turn it on
5. Connect the solar panel to the LiPo battery charger
6. Connect the charger to the LiPo battery
7. Set up the multimeter, set it to 6m amps to test the current

## 3.0 Testing Procedure

### 3.1 Car Test Procedure

1. Place the car onto the cleared out area on the ground.
2. Plug the LiPo Battery on the car in.
3. Press reset on the Arduino Nano.
4. The code on the Arduino will now begin cycling through the different states, causing the car to drive forward, backwards, and turn left and right.
5. Repeat this for the Car with the Elegoo Nano.

### 3.2 Controller Test Procedure

1. Test that left joystick controls the front left wheel
2. Test that right joystick controls the front right wheel

### 3.3 Charging Station Test Procedure

1. Connect the car battery to the charging station
2. Verify that the LEDs on the charging chip have lit up
3. Put the black test probe of the multimeter on the negative load out source and the red test probe to the positive load out source
4. Measure the voltage readings from the multimeter
5. Measure the current readings from the multimeter

## 4.0 Measurable Criteria

### 4.1 Car Testing Criteria

1. Each Car must be capable of driving forwards
2. Each Car must be capable of driving backwards
3. Each Car must be capable of turning left
4. Each Car must be capable of turning right
5. The Car with the LCD must display the battery level
6. The Components on each car must not fall off during operation.

If any of criteria 1-5 fail to be met, then the test is considered to be a failure.

### 4.2 Controller Testing Criteria

1. Joysticks must detect forwards and backwards inputs
2. Joysticks must shift between two different speeds and be able to stop
3. Joysticks must be able to cause the car to turn left and right
4. Controller must be able to control both cars
5. Controller must be able to switch between both cars

### 4.2 Charging Station Testing Criteria

1. The “ GOOD” green light of the LiPo battery charger should be on when it is connected to the solar panel
2. The “CHG” red light should be on when the LiPo battery charger is connected to the LiPo battery
3. When the multimeter is set up, the current measured should be 35mA

## 5.0 Scoring Sheets

### 5.1 Car Scoring Sheet

Test | Observed Result for Car 1 | Observed Results for Car 2 | Failure? (Y/N)

Driving Forward

Driving Backwards

Turning Left

Turning Right

Objects on Car Secure

LCD Display Battery State | | N/A

Overall Result:

### 5.2 Controller Scoring Sheet

Test | Observed Result | Failure? (Y/N)

Controller moves car forward and backwards

Controller switches between to different speeds and stop

Controller can send inputs for left and right turns

Controller can switch between the two cars

Overall Result:

### 5.3 Charging Station Scoring Sheet

Test | Observed Result | Failure? (Y/N)

LiPo Charger “Good” light color
should be green

LiPo Charger “Chg” light color should be red

Multimeter measurement of the current of the charger output

Overall Result:

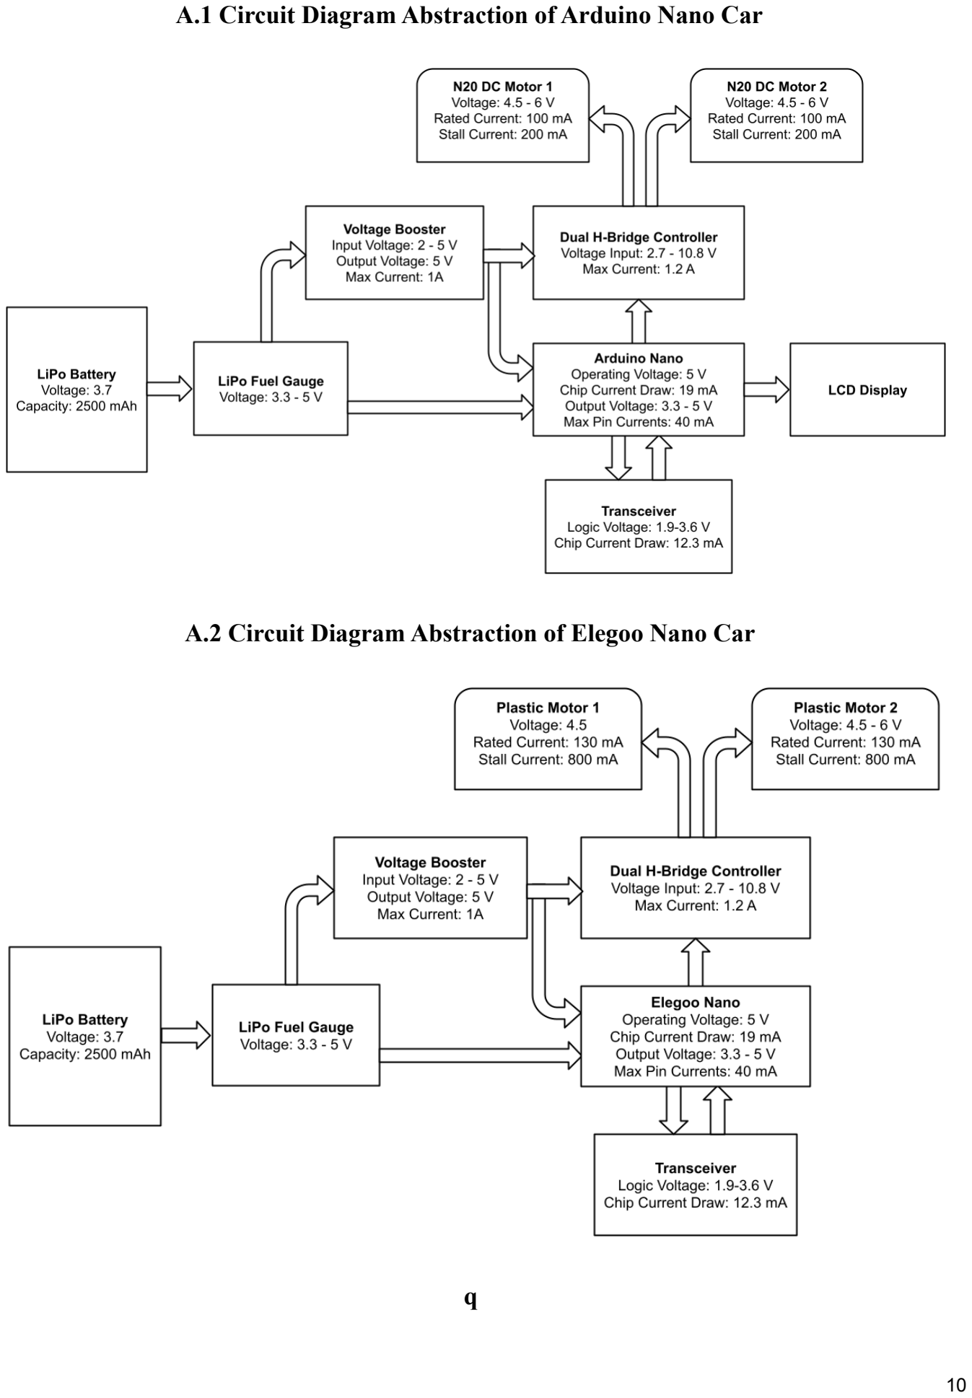
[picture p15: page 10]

A.1 Circuit Diagram Abstraction of Arduino Nano Car

A.2 Circuit Diagram Abstraction of Elegoo Nano Car

q

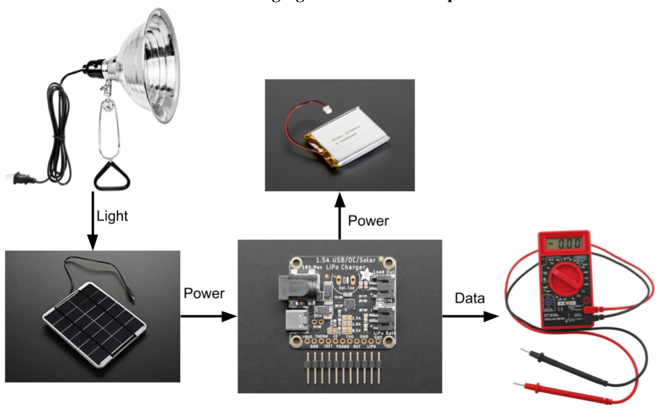
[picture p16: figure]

A.3 Charging Station Test Set-Up

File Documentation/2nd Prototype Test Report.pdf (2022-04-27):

# Memo

To: | Professor Pisano
From: | EV Builder Kit Team
Team: | 18
Date: | 03/18/22
Subject: | 2nd Prototype Testing Report

# Table of Contents

## 1.0 Summary of Equipment and Test Setup Pg 2

1.1) Car Summary
1.2) Controller Summary
1.3) Charging Station Summary
2.0 Measurements Taken | Pg 4
2.1) Car Measurements
2.2) Controller Measurements
2.3) Charging Station Measurements
3.0 Conclusions | Pg 7
3.1) Car Conclusion
3.2) Controller Conclusion
3.3) Charging Station Conclusion

## 1.0 Summary of Equipment and Test Setup

### 1.1 Car Summary

On each car, there is a 3.7 volt lithium polymer(LiPo) battery used to power the vehicle. This battery is attached to a LiPo fuel gauge chip, which is able to take in the LiPo Battery’s JST connector, and uses I2C to feed the Arduino Nano the battery life. connection. The fuel gauge chip also has output pins which are fed directly to a 5-volt Voltage Booster. The 5-volt voltage booster raises the 3.7 volt output from the battery to a 5 volt output, and feeds that voltage to power the Arduino Nano and dual H-Bridge motor controller. The motor controller is connected to two DC motors, while the Arduino Nano is connected to the motor controller. The Nano can then control the motors by applying Pulse Width Modulation(PWM) and shifting between logic high to logic low on the connections to the motor controller. A transceiver module is also attached to the Nano, allowing the external controller to control the signals sent to the motor controller, and thus control the motors as well.
On the larger car, an LCD display was also attached, along with the LiPo Charging chip. These were to showcase the fuel gauge’s ability to detect and send out the battery data, along with the capability to charge the battery by simply plugging in a provided DC jack to the charging chip. To set up the test, first connect each car’s Arduino Nano to a computer that has an autonomous testing code loaded onto it, then upload that code to the board. The autonomous code consists of commands that make the car cycle through driving forwards, turning left and right, then reversing. Once the code is uploaded, then disconnect the Arduino from the computer, and clear out an area for the car to begin driving on, and the car will begin cycling through the various driving states. The LCD and LiPo Charging Chip are not utilized for the testing of the car itself, and instead used to showcase the properties of the other components of this project.

### 1.2 Controller Summary

On the controller, there are 2 PS2 type axial joysticks, which are connected to an Arduino Uno. The Uno is able to take in the inputs from these joysticks, and use an attached transceiver chip to transmit a 3 bit message to the transceiver on the car. This allows the car to read the 3 bit message from the controller, and adjust its state accordingly.
To set up the test, first connect the car’s Arduino Nano to a computer that has the code for a receiver loaded onto it, then upload that code to the board. At the same time upload the controller code to an Arduino Uno. Once the code upload process is complete, place the car down onto a clear out area. This should enable the controller to control the car, with the car being able to drive forward, backwards, turn left and right, and speed based on the strength of the joysticks. The controller also had a toggle switch to let the user decide which car to use. The arduino detects if the switch has a high input which will indicate the switch is one to control one car and off to indicate another car. A complete controller will be able to control up to 3 cars if done correctly.

### 1.3.1 Charging Station Summary

For the charging station, there will be three main parts. Since our model will be indoors, an aluminum lamp with a hydroponic bulb is used to represent the sun. The hydroponic bulb mimics the visible light spectrum that would be expected from the sun, which is where most of the energy from the solar panels are derived. This lamp will be directed towards a solar panel, which is connected to a Lithium Polymer Charging Chip. This chip is capable of using the power from the solar panel to recharge the battery, while also load balancing to the output as well. The solar panel was mounted on a stand inside the kit at 45 degrees, which is the ideal degree. For this prototype, the main proof of concept is to show that using a lamp to power the solar panel is viable.
To set up the test, first plug in the lamp and clamp it on the edge of the kit. Turn the lamp towards the solar panel then connect the solar panel to the LiPo charging chip. The LiPo battery also has to be connected to the chip. To test the current and voltage, set the multimeter to 6m amps.

## 2.0 Measurements Taken

### 2.1 Car Measurements

### 5.1 Car Scoring Sheet

Test | Observed Result for Car 1 (Larger) | Observed Results for Car 2 | Failure? (Y/N)
Driving Forward | No Issue | No Issue | N
Driving Backwards | No Issue | No Issue | N
Turning Left | Smooth Turn, but slow | Slightly Jerky, but managed to turn | N
Turning Right | Smooth Turn, but slow | Smooth Turn | N
Objects on Car Secure | Yes | Yes | N
LCD Display Battery State | Visible, and active | N/A | N
| | Overall Result: | Successful

The tests showed that each car is able to drive itself forwards and backwards without any major issue. However, the process of turning was shaky for the smaller car, and slow for the bigger car. For the larger car, this slow turning was linked with a low battery, but nonetheless the turning was fine. As for the smaller car, the turning being shaky was linked to a lack of traction/torque for the car wheels. When additional weight was applied by pressing on the back of the car however, the turning was much smoother. At the same time none of the objects on the car fell apart during operation which indicates that the car is sturdy enough for operation. Additionally, when the LCD was tested, the proper data for battery life and mileage was displayed successfully, indicating that the fuel monitoring system works.

### 2.2 Controller Measurements

Controller Scoring Sheet

Test | Observed Result | Failure? (Y/N)
Controller moves car forward and backwards | Both joysticks when pressed forward made the car go forwards. Both joysticks when pressed backwards made the car go back. | N
Controller switches between to different speeds and stop | When the joysticks are slightly moved forward or backwards, the car moves slower. When the joysticks are moved all the way forward or backwards, the car moves faster. | N
Controller can switch between two different cars | A toggle switch is able to switch between 2 separate cars successfully and see the controller controlling both of them | N
Controller can send inputs for left and right turns | When joysticks were inverse of each other, the car moved slightly left or right. | N
Overall Result: | | Successful

The controller of the car was successful in delivering the inputs needed for the car to move. The car had to ultimately do 4 directions which were forward, backwards, left, and right. The joystick was able to make the car go within all these directions and have adjustable speed which is only two. The toggle switches were able to successfully switch between the two cars. However, the toggle switches seem to be damaged so an order of new switches were placed to solve the issue. The next step is to successfully mount the LCD to the controller to display relevant information of the car.

### 2.3 Charging Station Measurements

Charging Station Scoring Sheet

Test | Observed Result | Failure? (Y/N)
LiPo Charger “Good” light color should be green | The “Good” light turns green when the solar panel is connected to the chip. | N
LiPo Charger “Chg” light color should be red | The “Chg” light turns red when the LiPo battery is connected to the chip. | N
Multimeter measurement of the current of the charger output | When the multimeter is set up, the current measured should be 35mA | N
Overall Result: | | Successful

The test showed that the setup for the charging station successfully works. The “Good” and “Chg '' LED lights of the LiPo battery charging chip turned to the colors they were supposed to, so that it shows the chip is working and there is a flow of electricity in the model.
For our first test plan, we came into a problem with an incorrect current. We measured a current of 0.0071mA, but that was not the current that was charging the LiPo battery. To get the actual current of the battery, we will need to have a resistor in series with the output and then measure the current.
For this second test plan, we successfully received the correct current that was charging the Lipo battery. We estimated the charging time needed to completely charge the battery is around 20 minutes.

## 3.0 Conclusions

### 3.1 Car Conclusion

The results of the test show that the prototypes of cars are working as intended, and that the car is capable of driving, turning, and displaying key battery information without issue. This indicates that the circuitry selected for each car’s operation is working, and is proper for the final vehicles. This means that the circuits and hardware can be used for mass production. However, the car is not without flaws, as the car displayed some difficulty turning at the very beginning, and required additional weight applied to the back of the cars. So the electronics such as the microcontroller, control and transceiver chips, and motors are all functional and can be soldered directly onto the main breadboards for the final product. As for the body of the car, work must be done adding in weight and balancing the distribution on the prototypes, so that similar changes can be made to the final products to ensure that the car can turn properly.
The final steps for this part of the project is to create 4 more copies of the smaller car, adding in weight, and soldering all the components together. Once this is done, then the assembly of the cars is complete, and then the appearance of the car must be worked on. This entails creating a chassis, and making the entire car pleasant to look at.

### 3.2 Controller Conclusion

The results of the prototype testing were satisfactory because it accomplished everything that needed to be done. The controller is simple enough that any user can easily control the car. In addition, with the implementation of the switches, the controller is now able to control separate vehicles. Another thing the prototype showed was that the controller did not demonstrate portability which can be easily accomplished with a battery connected to the arduino. This is another thing that would be easily worked on. The last portion of the controller that needs to be complete is the visuals and successfully implementing the LCD which wouldn’t be too hard. The only problem that needs to be solved is to make the transmitters and receivers to transmit at the same time which needs further research. For the visuals we just need to find a shell of a controller so it can be comfortable for the users.

### 3.3 Charging Station Conclusion

The results of the test show that the charging chip works and the solar lamp is sufficient in providing enough energy for the smaller battery on the vehicles to be recharged. Our model is supposed to display how a real charging station works at a smaller scale, so the current should be strong enough to charge the battery in a small amount of time.
Moving forward we will work on the alternative charging method for the second charging station. For this second charging station, we might have an induction charging method or DC to AC charging method. We also need to focus on the visual aspect of the station.
For the first prototype, we made a wood stand (shown in Figure 1) and just put the solar panel on top of that. For this second prototype, we made the stand in the kit made of cardboard (shown in Figure 2) and just put it on top of it. For the lamp, we designed a detachable area under the solar panels (shown in Figure 3) so the kit can be more portable. This section of the kit will be mainly for charging stations and our EVs can drive in to recharge the batteries.

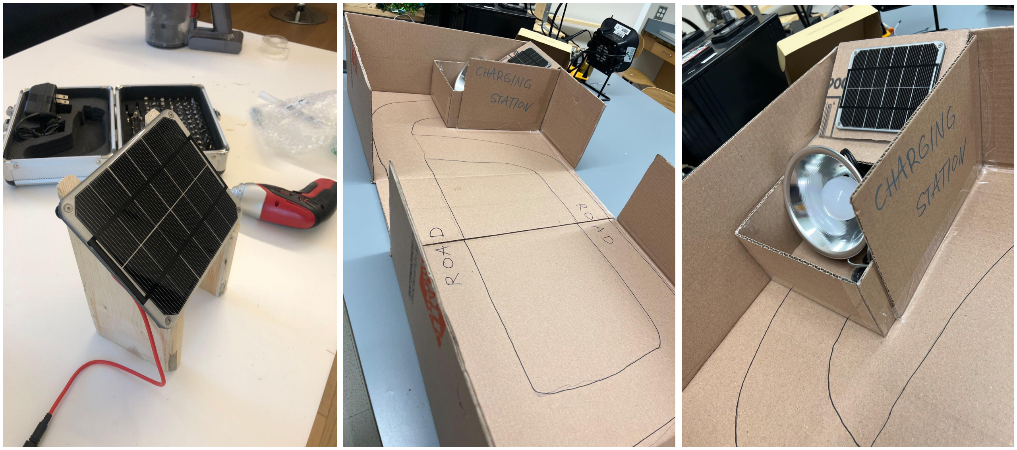
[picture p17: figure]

Figure. 1 | Figure.2 | Figure.3

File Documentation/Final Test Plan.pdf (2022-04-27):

# Memo

To: | Professor Pisano
From: | EV Builder Kit Team
Team: | 18
Date: | 03/31/22
Subject: | Final Testing Plan

# Table of Contents

1.0 Required Materials | Pg 2
1.1) Car Materials
1.2) Controller Materials
1.3) Charging Station Materials

## 2.0 Testing Setup and Explanation Pg 4

2.1) Introduction
2.2) Car Testing Setup
2.3) Controller Testing Setup
2.4) Charging Station Testing Setup
3.0 Testing Procedure - | Pg 6
3.1) Car Testing Procedure
3.2) Controller Testing Procedure
3.3) Charging Station Testing Procedure
4.0 Measurable Criteria | Pg 7
4.1) Car Testing Criteria
4.2) Controller Testing Criteria
4.3) Charging Station Criteria

## 5.0 Scoring Sheet & Appendix Pg 8

5.1) Car Scoring Sheet
5.2) Controller Scoring Sheet
5.3) Charging Station Scoring Sheet

## 1.0 Required Materials

### 1.1 Car Materials

Hardware Materials for the Heavy Duty Car
- Solderable Half Breadboard (2)
- Elegoo Nano (1)
- 3.7 Volt 500 mAH Lithium Polymer Battery (1)
- Dual H-Bridge Motor Controller (1)
- NRF24L01 Transceiver Chip (1)
- Adafruit LC709203F LiPoly Fuel Gauge (1)
- 5-Volt Voltage Booster Chip (1)
- N20 DC Motors and Mounts (2)
- Lego Cross Wheels (2)
- Standard Plastic 40mm Wheels (2)
- MDF Board
- PCB Screws
- 7 Gram Weights
- 22 AWG Wire of Assorted Colors and Wire Wrap Hardware Materials for each Light Duty Car
- Solderable Half Breadboards (2)
- Elegoo Nano (1)
- 3.7 Volt 500mAH Lithium Polymer Battery (1)
- Dual H-Bridge Motor Controller (1)
- NRF24L01 Transceiver Chip (1)
- Adafruit LC709203F LiPoly Fuel Gauge (1)
- 5-Volt Voltage Booster Chip (1)
- Pololu Plastic Motors and Mount(2)
- Pololu 32mm Plastic Wheels (2)
- Eudax Plastic Wheels (2)
- MDF Board (1)
- PCB Screws
- 7 Gram Weights
- 22 AWG Wire of Assorted Colors and Wire Wrap
Software Materials
- Arduino Script
- Read inputs from the controller and use that to drive forwards, backwards and turn.
- Read inputs from the fuel gauge chip, and send battery data via transceiver to display on the controller.

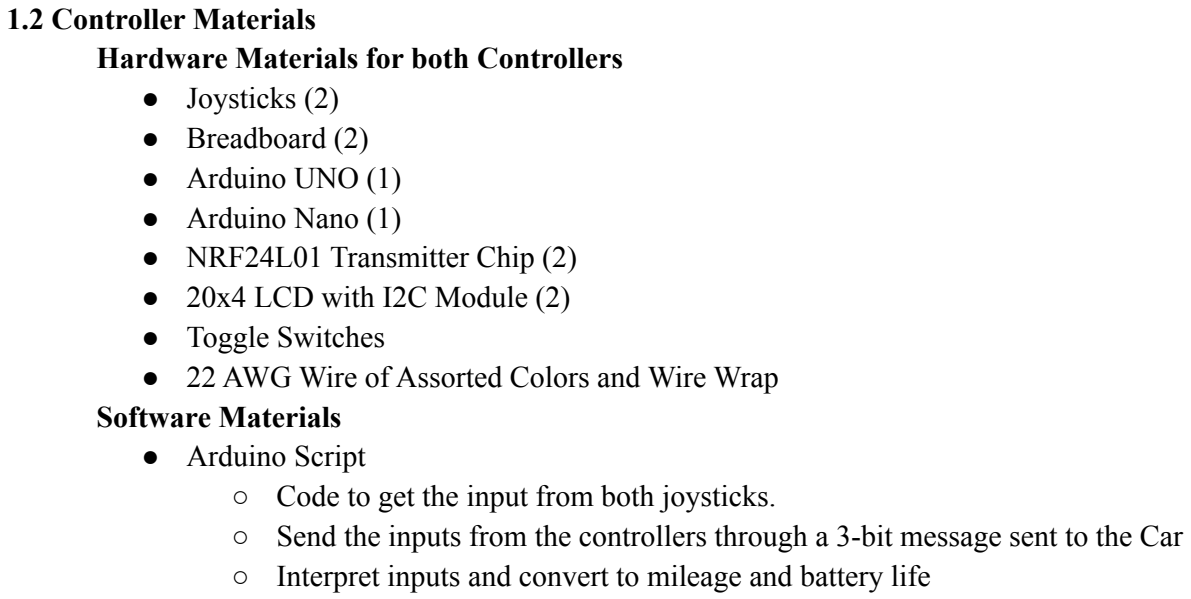
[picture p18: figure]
1.2 Controller Materials Hardware Materials for both Controllers ● Joysticks (2) ● Breadboard (2) ● Arduino UNO (1) ● Arduino Nano (1) ● NRF24L01 Transmitter Chip (2) ● 20x4 LCD with I2C Module (2) ● Toggle Switches; Software Materials ● Arduino Script

- 22 AWG Wire of Assorted Colors and Wire Wrap
- Code to get the input from both joysticks.
- Send the inputs from the controllers through a 3-bit message sent to the Car
- Interpret inputs and convert to mileage and battery life

### 1.3 Charging Station Materials

Hardware Materials
- Cardboard Stand (1)
- 6V 2W Solar Panel (1)
- 5.5’Aluminum Reflector Lamp (1)
- 9W Hydroponic Bulb (1)
- Wood Light Stand (1)
- Li-Po Battery Charging Circuit Chip (1)
- 3.7 Volt Lithium Polymer (LiPo) Battery (1)
- Digital Multimeter (1)
- Industrial cardboards

## 2.0 Testing Setup and Explanation

### 2.1 Introduction

The tests can be split up into three categories: testing the cars, testing the controllers, and testing the charging station. The cars act as the main body of interest for all three of these tests, as they are set up with motors, transceivers, and a battery. This allows the car to interact with the charging station and controller, and produce visible outputs from the test directly.

Car:
On each car, there is a 3.7 volt lithium polymer (LiPo) battery which is used to power the vehicle. This battery is attached to a LiPo fuel gauge chip, which is able to take in a LiPo Battery connection. The fuel gauge chip has output pins which are fed directly to the Arduino Nano, as well as into a 5-Volt Voltage Booster. The direct feed to the Arduino Nano is for the purpose of measuring battery state, sending that data to the transceiver, so that it can be displayed properly on the Controller’s LCD display. The 5-Volt voltage booster raises the 3.7 volt output from the battery to a 5 volt output, and feeds that voltage to power the Arduino Nano and dual H-Bridge motor controller. The motor controller is connected to two DC motors, while the Arduino Nano is connected to the motor controller. The Nano can then control the motors by applying Pulse Width Modulation(PWM) and shifting between logic high to logic low on the connections to the motor controller. A transceiver module is also attached to the Nano, allowing an external controller to control the signals sent to the motor controller, and thus the motors from there. Additionally the Nano will also use the transceiver to send the battery data to display on the controllers.

Controller:
On the controller, there are 2 axial joysticks, which are connected to an Arduino Uno. The uno is able to take in the inputs from these joysticks, and use an attached transceiver chip to transmit an 3 bit message to the transceiver on the car. This allows the car to read the 3 bit message from the controller, and adjust its state accordingly. Furthermore, the controller will have a toggle switch you use to switch between which car you want to control. There is an LCD attached to the controller displaying the miles and battery life of the car being driven.

Charging Station:
For the solar charging station, an aluminum lamp with a hydroponic bulb is used. This is as the hydroponic bulb mimics the visible light spectrum that would be expected from the sun, which is where most of the energy from the solar panels are derived. This lamp will be directed towards a solar panel, which is connected to a Lithium Polymer Charging Chip. This chip is capable of using the power from the solar panel to recharge the battery, while also load balancing to the output as well. Additionally a DC adapter and a USB-C cable can also interface with this chip to provide power as well.

### 2.2 Car Pre-Testing Setup

1. Connect the assorted Nanos to a computer with the correct addressed code loaded onto it
2. Upload the code from the computer to the Arduino Nano
3. Disconnect the computer from the Arduino Nano
4. Clear out an area on the ground for the car to operate on
5. Repeat steps 1-4 with each car.

### 2.3 Controller Pre-Testing Setup

1. Connect the Controller Microcontrollers to the computer for power.
2. Upload the code onto the Arduinos of each controller
3. Toggle the switches to select the initial cars for use.

### 2.4 Charging Station Pre-Testing Setup

1. Solar lamp is stored in the kit for portable use
2. Take the solar lamp out and clamp it on the side of the kit
3. The kit wall is able to hold the weight of the lamp
4. Turn the lamp towards the solar panel.
5. Plug the DC Adapter into the wall outlet, and fit the correct DC jack.
6. Connect the USB-C Cable to the USB Power Supply

## 3.0 Testing Procedure

### 3.1 Car and Controller Test Procedure

1. Place the car onto the cleared out area on the ground.
2. Switch on the power switch.
3. Test that left joystick controls the front left wheel
4. Test that right joystick controls the front right wheel
5. Test that the cars are properly sending battery data to the controller, and is being displayed

### 3.2 Charging Station Test Procedure

1. Connect the cars to the Solar Charging station.
2. Turn on the Solar Lamp
3. Disconnect the Solar Charging station, and plug in the DC adapter
4. Disconnect the DC adapter and plug in the USB-C Cable.
5. Verify that the LEDs on the charging chip have lit up in each case.

## 4.0 Measurable Criteria

### 4.1 Car Testing Criteria

1. Each Car must be capable of driving forwards
2. Each Car must be capable of driving backwards
3. Each Car must be capable of turning left
4. Each Car must be capable of turning right
5. The Components on each car must not fall off during operation.

If any of criteria 1-5 fail to be met, then the test is considered to be a failure.

### 4.2 Controller Testing Criteria

1. Joysticks must detect forwards and backwards inputs
2. Joysticks must be able to cause the car to turn left and right
3. Controller must be able to switch between both cars
4. When no inputs are sent, cars should stop
5. LCD shows the miles and battery level

### 4.2 Charging Station Testing Criteria

1. The “ GOOD” green light of the LiPo battery charger should be on when it is connected to any power supply.
2. The “CHG” red light should be on when the LiPo battery charger is connected to a LiPo battery that is not fully charged.

## 5.0 Scoring Sheets

### 5.1 Car Scoring Sheet

Test | Observed Result for HDV | Observed Results for LDVs 1-5 | Failure? (Y/N)

Driving Forward

Driving Backwards

Turning Left

Turning Right

Objects on Car Secure

Overall Result:

### 5.2 Controller Scoring Sheet

Test | Controller 1 | Controller 2 | Failure? (Y/N)

Controller moves car forward and backwards

Controller can send inputs for left and right turns

Controller can switch between the two cars

When controller untouched, cars should stop

LCD is displaying the miles and battery life

Overall Result:

### 5.3 Charging Station Scoring Sheet

Test | Solar | DC Adaptor | USB-C | Failure? (Y/N)

LiPo Charger “Good” light color should be green

LiPo Charger “Chg” light color should be red

Overall Result:

A.1 Circuit Diagram Abstraction of Heavy Duty Vehicle

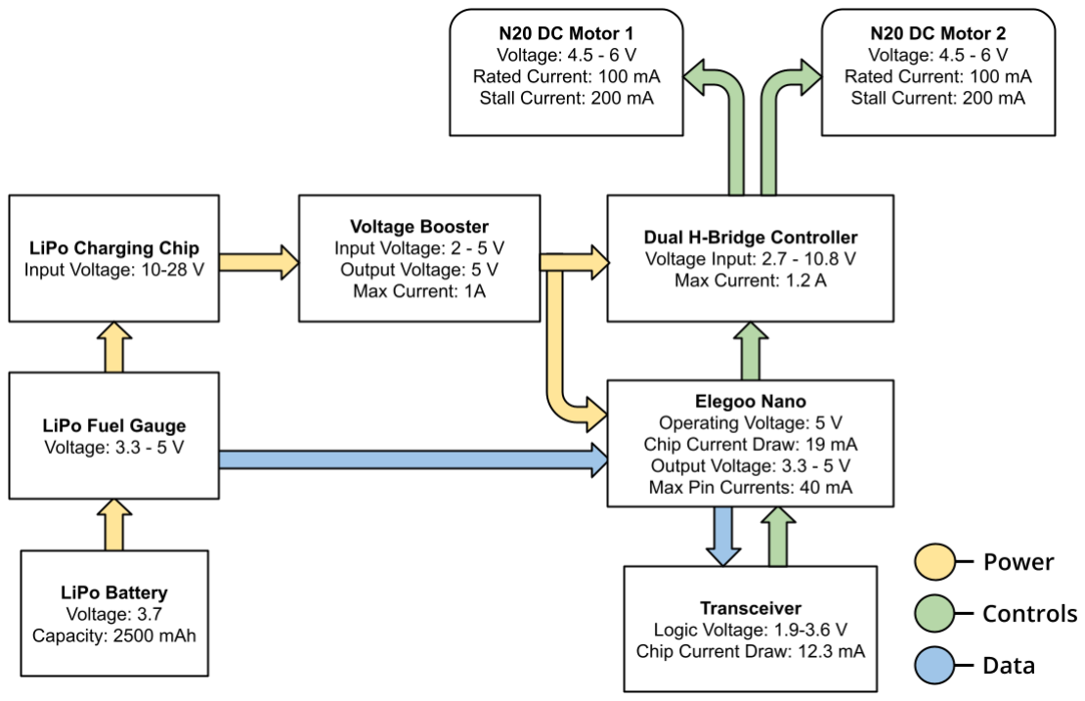
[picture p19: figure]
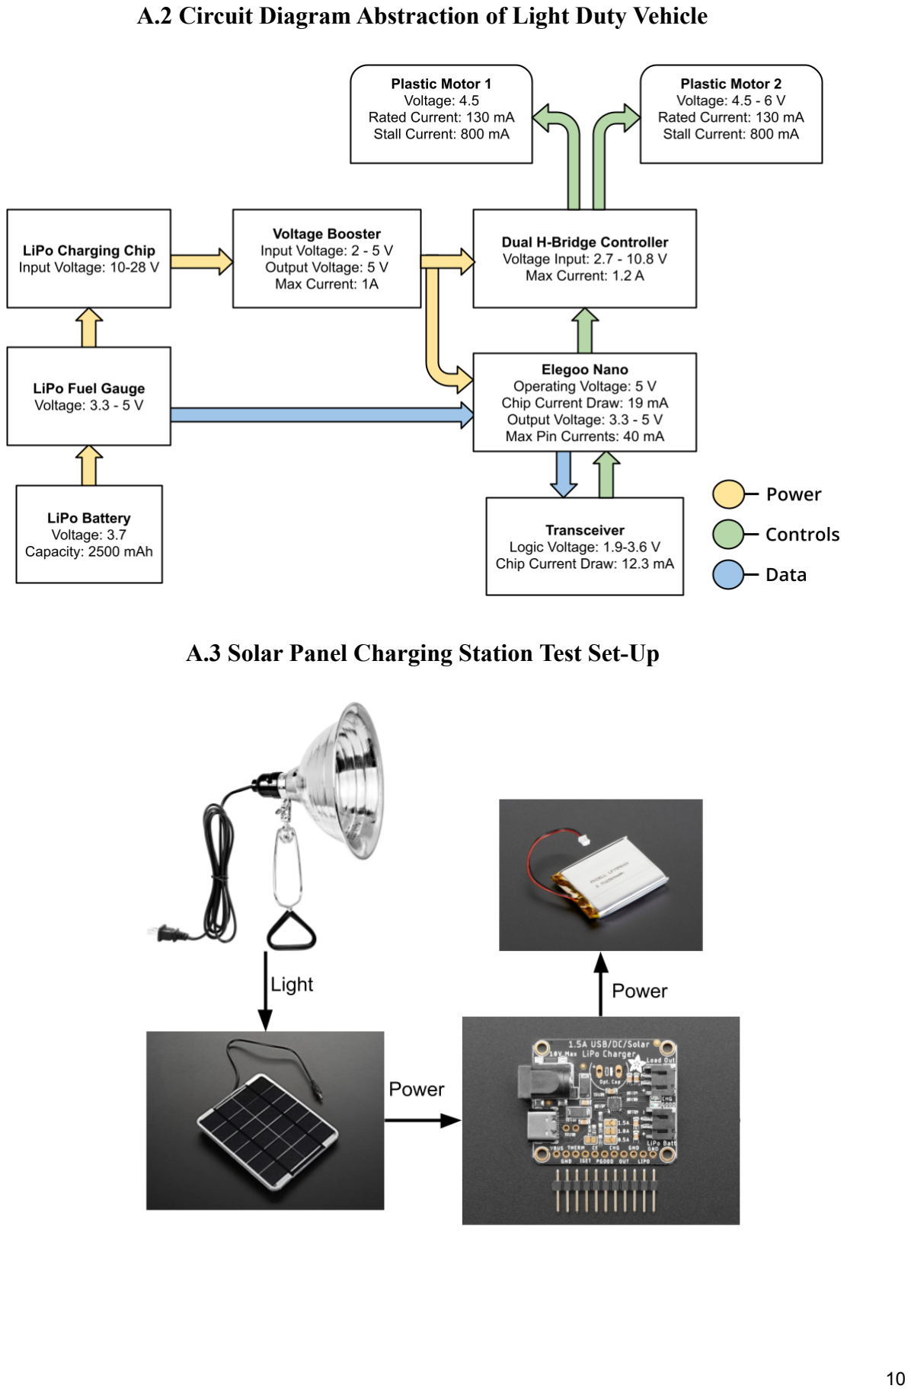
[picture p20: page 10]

A.2 Circuit Diagram Abstraction of Light Duty Vehicle

A.3 Solar Panel Charging Station Test Set-Up

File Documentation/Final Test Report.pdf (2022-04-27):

# Memo

To: | Professor Pisano
From: | EV Builder Kit Team
Team: | 18
Date: | 04/07/22
Subject: | Final Prototype Testing Report

# Table of Contents

## 1.0 Summary of Equipment and Test Setup Pg 2

1.1) Car Summary
1.2) Controller Summary
1.3) Charging Station Summary
2.0 Measurements Taken | Pg 4
2.1) Car Measurements
2.2) Controller Measurements
2.3) Charging Station Measurements
3.0 Conclusions | Pg 7
3.1) Car Conclusion
3.2) Controller Conclusion
3.3) Charging Station Conclusion

## 1.0 Summary of Equipment and Test Setup

### 1.1 Car Summary

On each car, there is a 3.7 volt lithium polymer (LiPo) battery which is used to power the vehicle. This battery is attached to a LiPo fuel gauge chip, which is able to take in a LiPo Battery connection. The fuel gauge chip has output pins which are fed directly to the Arduino Nano, as well as into a 5-Volt Voltage Booster. The direct feed to the Arduino Nano is for the purpose of measuring battery state, sending that data to the transceiver, so that it can be displayed properly on the Controller’s LCD display. The 5-Volt voltage booster raises the 3.7 volt output from the battery to a 5 volt output, and feeds that voltage to power the Arduino Nano and dual H-Bridge motor controller. The motor controller is connected to two DC motors, while the Arduino Nano is connected to the motor controller. The Nano can then control the motors by applying Pulse Width Modulation(PWM) and shifting between logic high to logic low on the connections to the motor controller. A transceiver module is also attached to the Nano, allowing an external controller to control the signals sent to the motor controller, and thus the motors from there. Additionally the Nano will also use the transceiver to send the battery data to display on the controllers.
A special heavy duty car was also created, utilizing larger wheels and more added on weights, but is functionally and electrically identical to the other cars created for the test.
To set up the test, first connect each car’s microcontroller to a computer that has appropriate code for transmitting battery data and receiving controller input loaded onto it, then upload that code to the board. The computer will require the CH340 driver to be able to interface with the microcontrollers attached to the cars. Once the code is uploaded to each controller, then disconnect the Arduino from the computer, and clear out an area for the car to begin driving on.

### 1.2 Controller Summary

On each of the two controllers, there are 2 axial joysticks, which are connected to an Arduino Uno. The uno is able to take in the inputs from these joysticks, and use an attached transceiver chip to transmit an 3 bit message to the transceiver on the car. This allows the car to read the 3 bit message from the controller, and adjust its state accordingly. Furthermore, the controller will have a toggle switch you use to switch between which car you want to control. There is also an LCD attached to the controller displaying the miles and battery life of the car being driven.
To set up the test, first connect the car’s Arduino Nano to a computer that has the code for a receiver loaded onto it, then upload that code to the board. At the same time upload the controller code to an Arduino Uno. Once the code upload process is complete, place the car down onto a clear out area. This should enable the controller to control the car, with the car being able to drive forward, backwards, turn left and right, and speed based on the strength of the joysticks. The controller also has multiple toggle switches to let the user decide which of three connected cars to interface with. The controller detects the state of each switch, and uses that to change the communication address for the controller’s transceiver.

### 1.3.1 Charging Station Summary

For the solar charging station, an aluminum lamp with a hydroponic bulb is used. This is as the hydroponic bulb mimics the visible light spectrum that would be expected from the sun, which is where most of the energy from the solar panels are derived. This lamp will be directed towards a solar panel, which is connected to a Lithium Polymer Charging Chip. This chip is capable of using the power from the solar panel to recharge the battery, while also load balancing to the output as well. Additionally a DC adapter and a USB-C cable can also interface with this chip to provide power as well.
To set up the test, first plug in the lamp and clamp it on the edge of the kit. Turn the lamp towards the solar panel then connect the solar panel to the LiPo charging chip attached to the cars. The LiPo battery also has to be connected to the cars as well for the test to proceed. After verifying that charging occurs utilizing the solar panel setup, ensure that the same holds true using a DC wall plug adapter, and a USB type c cable.

## 2.0 Measurements Taken

### 2.1 Car Measurements

### 5.1 Car Scoring Sheet

Test | Observed Result for HDV | Observed Results for LDVs 1-5 | Failure? (Y/N)
Driving Forward | No Issue | No Issue | N
Driving Backwards | No Issue | No Issue | N
Turning Left | No Issue | No Issue | N
Turning Right | No Issue | No Issue | N
Objects on Car Secure | Yes | Yes | N
| | Overall Result: | Successful

The tests showed that each car was able to drive itself forwards and backwards without any major issue, and that the process of turning was smooth for each vehicle. Due to the fact that the turning and driving of the car was successful, it can be seen that the power systems, transceiver set-up, and mechanical makeup of the cars are all functionally sound, and able to support all of the requirements. Thus the tests show that the cars by themselves should be fine. One issue that did come up during the testing was that cars would occasionally go haywire, but that is discussed in the next section, and is believed to be an issue with the controller setup.

### 5.2 Controller Scoring Sheet

Test | Controller 1 | Controller 2 | Failure? (Y/N)
Controller moves car forward and backwards | No Issue | No Issue | N
Controller can send inputs for left and right turns | No Issue | No Issue | N
Controller can switch between the three linked cars | No Issue | No Issue | N
When controller untouched, cars should stop | No Issue | Issue | N
LCD is displaying the miles and battery life | No Mileage | No Mileage | N
| | Overall Result: | Successful

Each of the controllers were successful in driving all three of the associated vehicles forwards, backwards, and turning. This indicates that the joysticks and toggle switches that are being used are functionally sound, and are providing the inputs required for the control logic to proceed as planned. Additionally each of the LCDs were able to display battery life info, and change that information upon a swap between vehicles, indicating that the controller is also properly receiving the data from the car. However there were two issues that were encountered during the test, which should be easy fixes. The first issue is that occasionally one of the cars being controlled will go haywire, and either shut off or get stuck in an infinite loop. This is because the connections that are being used on the controller are susceptible to static electricity, which overloads the transceiver, thus sending faulty information to the car controllers and causing an exception in the car code. The other issue was that mileage calculations were not implemented, as there was an error in the software that would cause the entire system to die when mileage was being displayed, and could not be remedied by the time of the test. However the controllers are shown to be working.

### 2.3 Charging Station Measurements

### 5.3 Charging Station Scoring Sheet

Test | Solar | DC Adaptor | USB-C | Failure? (Y/N)
LiPo Charger “Good” light color should be green | Y | Y | Y | N
LiPo Charger “Chg” light color should be red | Y | Y | Y | N
Overall Result: | | | | Successful

The test showed that the setup for the charging station successfully works. The “Good” and “Chg '' LED lights of the LiPo battery charging chip turned to the colors they were supposed to, so that it shows the chip is working and there is a flow of electricity going through to the car and recharging the battery in all three scenarios. This indicates that the charging methods we are planning to use in for this model are all valid, and can be utilized.

## 3.0 Conclusions
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

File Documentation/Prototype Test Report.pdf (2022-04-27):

# Memo

To: | Professor Pisano
From: | EV Builder Kit Team
Team: | 18
Date: | 11/21/21
Subject: | Prototype Testing Report

# Table of Contents

## 1.0 Summary of Equipment and Test Setup Pg 2

1.1) Car Summary
1.2) Controller Summary
1.3) Charging Station Summary
2.0 Measurements Taken | Pg 4
2.1) Car Measurements
2.2) Controller Measurements
2.3) Charging Station Measurements
3.0 Conclusions | Pg 7
3.1) Car Conclusion
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

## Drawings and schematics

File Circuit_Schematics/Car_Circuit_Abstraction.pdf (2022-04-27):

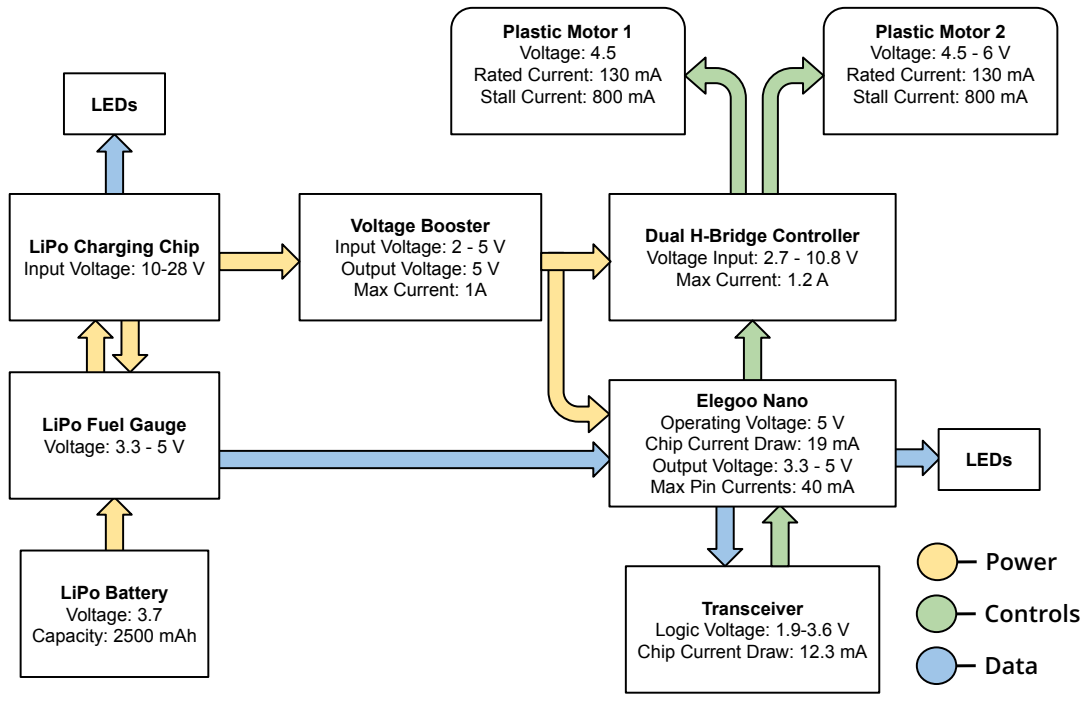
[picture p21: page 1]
LiPo Battery Voltage: 3.7 Capacity: 2500 mAh; Voltage Booster Input Voltage: 2 - 5 V Output Voltage: 5 V Max Current: 1A; Data; Power; Controls; LEDs

Plastic Motor 1
Voltage: 4.5
Rated Current: 130 mA
Stall Current: 800 mA

Plastic Motor 2
Voltage: 4.5 - 6 V

Dual H-Bridge Controller
Voltage Input: 2.7 - 10.8 V
Max Current: 1.2 A

LiPo Charging Chip
Input Voltage: 10-28 V

Elegoo Nano
Operating Voltage: 5 V
Chip Current Draw: 19 mA
Output Voltage: 3.3 - 5 V
Max Pin Currents: 40 mA

LiPo Fuel Gauge
Voltage: 3.3 - 5 V

Transceiver
Logic Voltage: 1.9-3.6 V
Chip Current Draw: 12.3 mA

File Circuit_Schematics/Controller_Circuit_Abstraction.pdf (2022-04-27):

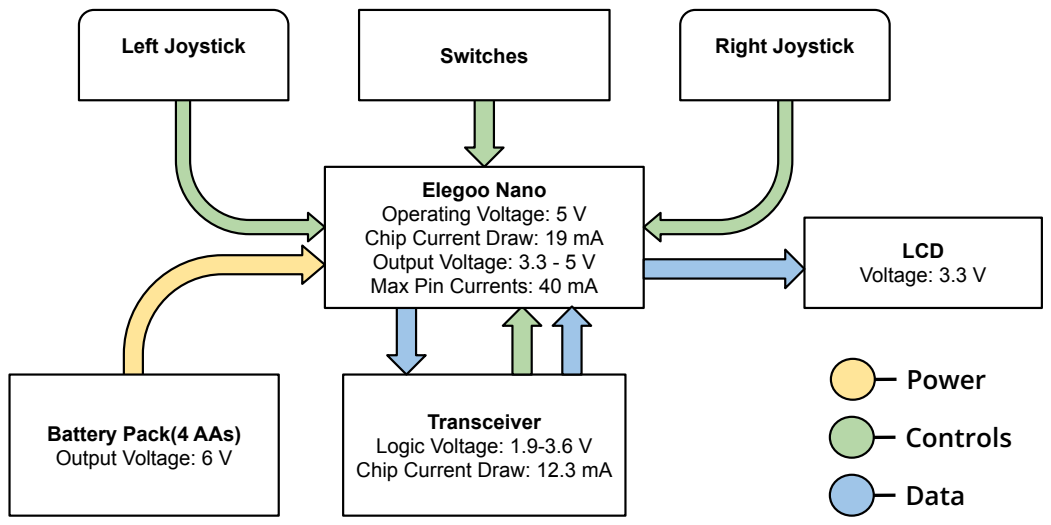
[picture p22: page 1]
Data; Power; Battery Pack(4 AAs); Controls; Output Voltage: 6 V; Switches Left Joystick; Right Joystick; LCD Voltage: 3.3 V

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

Transceiver
Logic Voltage: 1.9-3.6 V
Chip Current Draw: 12.3 mA

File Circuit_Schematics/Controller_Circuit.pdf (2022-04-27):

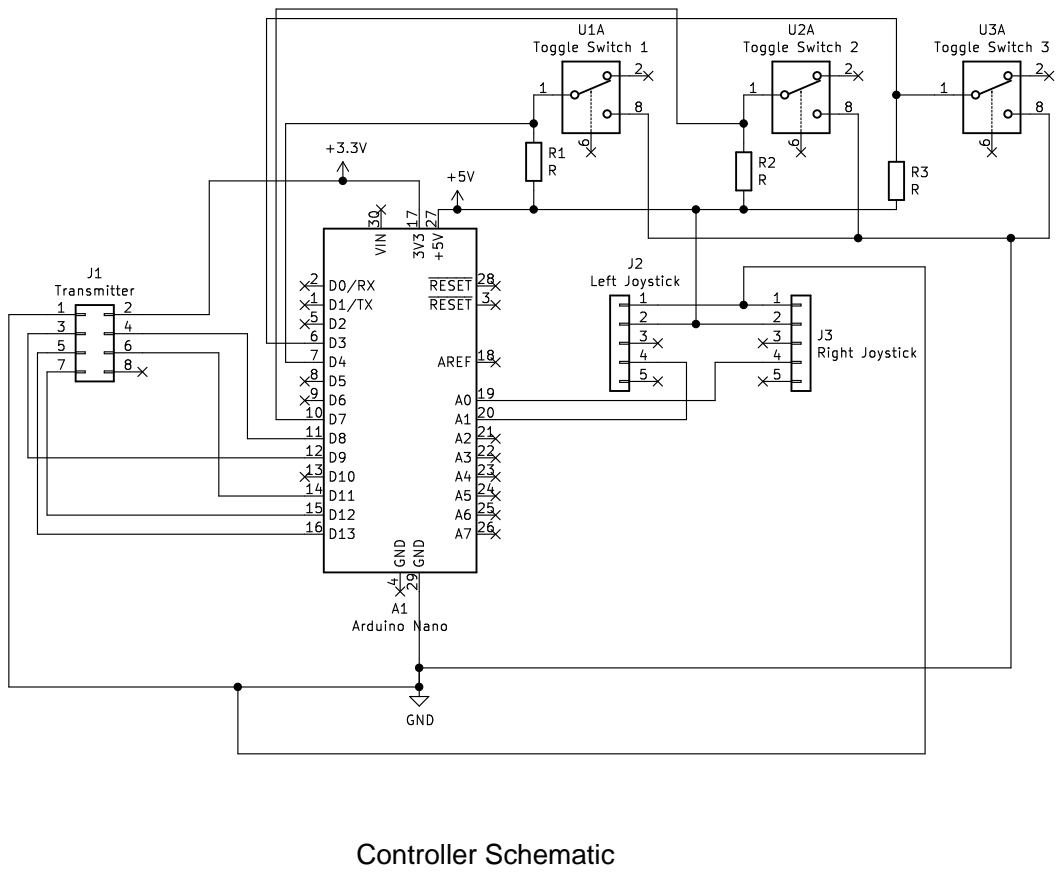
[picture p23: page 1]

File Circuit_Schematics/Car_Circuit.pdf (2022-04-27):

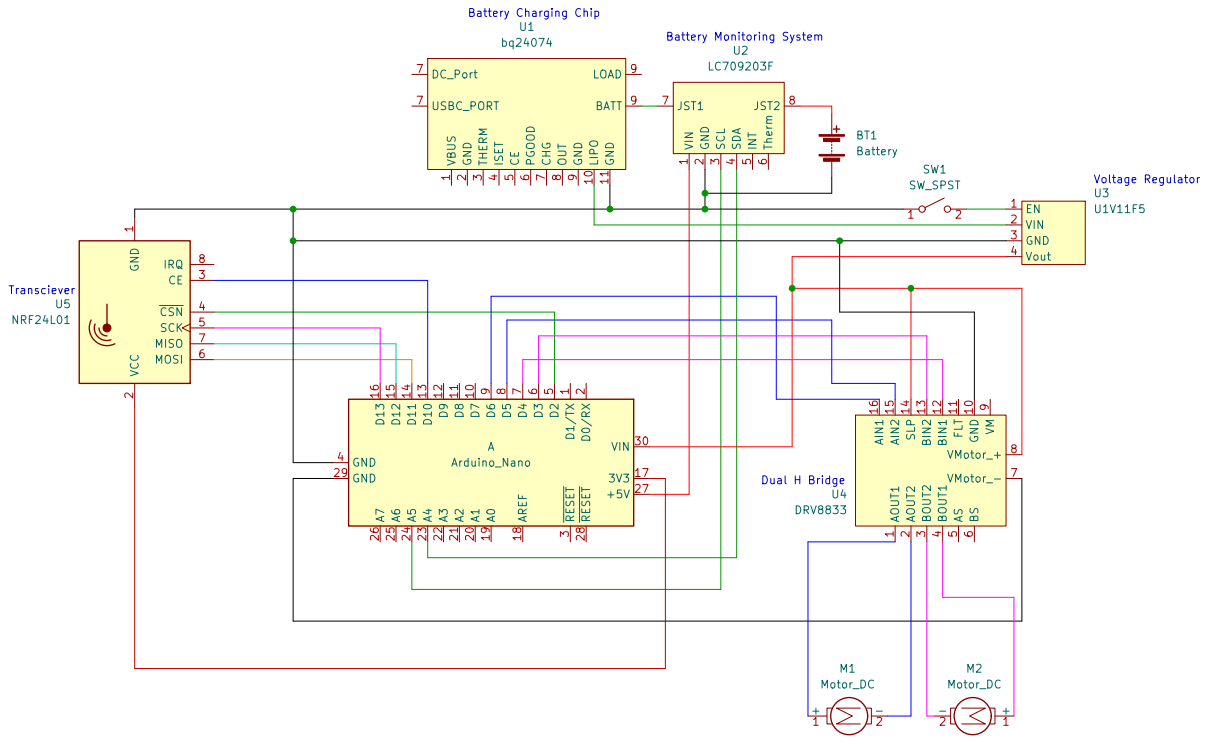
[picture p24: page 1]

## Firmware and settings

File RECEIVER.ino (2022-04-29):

#include "Adafruit_LC709203F.h"
#include <SPI.h>
#include <nRF24L01.h>
#include <RF24.h>

int ReceivedMessage[1] = {000};
RF24 radio(10, 2);
const byte address[6] = "00100";
char POWER[8] = "";

//Defining the State of Charge Board
Adafruit_LC709203F lc;
//Defining Pins that control the motors
#define Motor1P1 3
#define Motor1P2 4
#define Motor2P2 5
#define Motor2P1 6
//Defining the LED to signify Controller Communication
#define On 8

void setup() {
  
  radio.begin();

  //set the address
  radio.openReadingPipe(0, address);

  //Set module as receiver
  radio.startListening();

  
  Serial.begin(115200);
  delay(10);
  Serial.println("\nMotor And Battery Demo");
  if (!lc.begin()) {
    Serial.println(F("Couldnt find Adafruit LC709203F?\nMake sure a battery is plugged in!"));
    while (1) delay(10);
  }
  Serial.println(F("Found LC709203F"));
  Serial.print("Version: 0x"); Serial.println(lc.getICversion(), HEX);
  lc.setThermistorB(3950);
  lc.setPackSize(LC709203F_APA_500MAH);

  //Set Output Mode for the Pins
  pinMode(Motor1P1, OUTPUT);
  pinMode(Motor1P2, OUTPUT);
  pinMode(Motor2P1, OUTPUT);
  pinMode(Motor2P2, OUTPUT);
  pinMode(On,OUTPUT);
}

void loop() {
  while (radio.available()) {
    // If Radio Pipe Open = Controller Communicating
    digitalWrite(On, HIGH);
    radio.read(ReceivedMessage, 1);

    if (ReceivedMessage[0] == 001) {
      // Both Motors Running Forward Fast
      digitalWrite(Motor1P1, HIGH);
      digitalWrite(Motor1P2, LOW);
      digitalWrite(Motor2P1, HIGH);
      digitalWrite(Motor2P2, LOW);
      analogWrite(Motor1P1,255);
      analogWrite(Motor2P1,255);
    }
    
    if (ReceivedMessage[0] == 010) {
      // Both Motors Running Forward Slower
      digitalWrite(Motor1P1, HIGH);
      digitalWrite(Motor1P2, LOW);
      digitalWrite(Motor2P1, HIGH);
      digitalWrite(Motor2P2, LOW);
      analogWrite(Motor1P1,125);
      analogWrite(Motor2P1,125);
    }
    
    if (ReceivedMessage[0] == 000) {
      // Both Motors Off
      digitalWrite(Motor1P1, LOW);
      digitalWrite(Motor1P2, LOW);
      digitalWrite(Motor2P1, LOW);
      digitalWrite(Motor2P2, LOW);
    }

    if (ReceivedMessage[0] == 100){
      // Both Motors Running Reverse Fast
      digitalWrite(Motor1P1, LOW);
      digitalWrite(Motor1P2, HIGH);
      digitalWrite(Motor2P1, LOW);
      digitalWrite(Motor2P2, HIGH);
      analogWrite(Motor1P2,255);
      analogWrite(Motor2P2,255);
    }
    
    if (ReceivedMessage[0] == 011) {
      // Both Motors Running Reverse Slower
      digitalWrite(Motor1P1, LOW);
      digitalWrite(Motor1P2, HIGH);
      digitalWrite(Motor2P1, LOW);
      digitalWrite(Motor2P2, HIGH);
      analogWrite(Motor1P2,125);
      analogWrite(Motor2P2,125);
    }

    if (ReceivedMessage[0] == 101){
      // TURN LEFT
      digitalWrite(Motor1P1, LOW);
      digitalWrite(Motor1P2, HIGH);
      digitalWrite(Motor2P1, HIGH);
      digitalWrite(Motor2P2, LOW);
      analogWrite(Motor1P2,255);
      analogWrite(Motor2P1,255);
    }

    if (ReceivedMessage[0] == 110){
      // TURN RIGHT
      digitalWrite(Motor1P1, HIGH);
      digitalWrite(Motor1P2, LOW);
      digitalWrite(Motor2P1, LOW);
      digitalWrite(Motor2P2, HIGH);
      analogWrite(Motor1P1,255);
      analogWrite(Motor2P2,255);
    }

    if (ReceivedMessage[0] == 111) {
      radio.begin();
      radio.openWritingPipe(address);
      radio.stopListening();

      dtostrf(lc.cellPercent(), 6, 2, POWER);
      radio.write(&POWER, sizeof(POWER));

      radio.begin();
      radio.openReadingPipe(0, address);
      radio.startListening();
  }

  }
  digitalWrite(On, LOW);
}

void transmitter(const byte stuff, float batt, int msg[0]) {
  char battery[8] = "";
  
  if (msg[0] == 111) {
    Serial.println("RECEIVED");
    radio.begin();
    radio.openWritingPipe(stuff);
    radio.stopListening();

    dtostrf(batt, 6, 2, battery);
    radio.write(&battery, sizeof(battery));

    radio.begin();
    radio.openReadingPipe(0, stuff);
    radio.startListening();
  }
  return;
}

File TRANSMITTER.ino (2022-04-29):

#include <LiquidCrystal_I2C.h>
#include <nRF24L01.h>
#include <printf.h>
#include <RF24.h>
#include <RF24_config.h>
#include <SPI.h>

// Sets up the radio using pins 9 and 8
RF24 radio(9, 8);
// Sets up the LCD to display information
LiquidCrystal_I2C lcd(0x27, 20, 4);
// Different Addresses for vehicles, each controller has 3 vehicles attached to it.
const byte vehicle_1[6] = "00011";
const byte vehicle_2[6] = "00100";
const byte vehicle_3[6] = "00110";
/////////////////////////////////////////////////////////////////////////////
byte vehicle[6] = "00000";
int yPosition_1 = 0;
int xPosition_2 = 0;
int Switch_1;
int Switch_2;
int Switch_3;
long timer = 0;
float miles_1 = 149.00;
float miles_2 = 149.00;
float miles_3 = 149.00;

int SentMessage[1] = {000};

void setup() {
  Serial.begin(19200);
  pinMode(A0, INPUT);
  pinMode(A1, INPUT);
  pinMode(2, OUTPUT);
  pinMode(3, INPUT);
  pinMode(4, INPUT);
  pinMode(7, INPUT);
  lcd.begin();
  lcd.setCursor(0,0);
  lcd.print("Nissan Leaf S");
  lcd.setCursor(0,2);
  lcd.print("Miles: ");
//  lcd.setCursor(0,3);
//  lcd.print("Actual Battery:");
  
}

void loop() {
  yPosition_1 = analogRead(A0);
  xPosition_2 = analogRead(A1);
  Switch_1 = digitalRead(4);
  Switch_2 = digitalRead(7);
  Switch_3 = digitalRead(3);
  
//////////////////////////////////////////////////////////////////////////////////////////
//Toggle Switches to decide which vehicle the user will manage

  switch (Switch_1) {
    case 1:
      lcd.setCursor(0,0);
      lcd.print("Nissan Leaf S (1)");
      radio.begin();
      radio.openWritingPipe(vehicle_1);
      radio.stopListening();
      if ((timer % 10) == 0) {
      //  Serial.println(timer);
      //  switch_to_receiver(vehicle_1);
        miles_1 = miles_1 - 1;
      }
        lcd.setCursor(8,2);
        lcd.print(miles_1);
        while(miles_1 < 1) {
          miles_1 = 0;
          lcd.setCursor(6,2);
          lcd.print("NEEDS CHARGING");
          SentMessage[0] = 000;
          radio.write(SentMessage, 1);
          Serial.println(Switch_1);
          Switch_1 = digitalRead(4);
          if (Switch_1 != 1) {
            lcd.clear();
            lcd.setCursor(0,0);
            lcd.print("Nissan Leaf S");
            lcd.setCursor(0,2);
            lcd.print("Miles: ");
            break;
          }
        }
      //Serial.println("00011");
      break;
      
    case 0:
      break;
  }

  switch (Switch_2 == 1) {
    case 1:
      lcd.setCursor(0,0);
      lcd.print("Nissan Leaf S (2)");
      radio.begin();
      radio.openWritingPipe(vehicle_2);
      radio.stopListening();
      if ((timer % 500) == 0) {
      //  Serial.println(timer);
      //  switch_to_receiver(vehicle_2);
        miles_2 = miles_2 - 1;
      }
        lcd.setCursor(8,2);
        lcd.print(miles_2);
        while(miles_2 < 1) {
          miles_2 = 0;
          lcd.setCursor(6,2);
          lcd.print("NEEDS CHARGING");
          SentMessage[0] = 000;
          radio.write(SentMessage, 1);
          Serial.println(Switch_2);
          Switch_3 = digitalRead(2);
          if (Switch_2 != 1) {
            lcd.clear();
            lcd.setCursor(0,0);
            lcd.print("Nissan Leaf S");
            lcd.setCursor(0,2);
            lcd.print("Miles: ");
            break;
          }
        }
      //Serial.println("00100");
      break;

    case 0:
      break;
  }
  
  switch (Switch_3 == 1) {
    case 1:
      lcd.setCursor(0,0);
      lcd.print("Nissan Leaf S (3)");
      radio.begin();
      radio.openWritingPipe(vehicle_3);
      radio.stopListening();
      if ((timer % 250) == 0) {
      //  Serial.println(timer);
      //  switch_to_receiver(vehicle_3);
        miles_3 = miles_3 - 1;
      }
        lcd.setCursor(8,2);
        lcd.print(miles_3);
        while(miles_3 < 1) {
          miles_3 = 0;
          lcd.setCursor(6,2);
          lcd.print("NEEDS CHARGING");
          SentMessage[0] = 000;
          radio.write(SentMessage, 1);
          Serial.println(Switch_3);
          Switch_3 = digitalRead(3);
          if (Switch_3 != 1) {
            lcd.clear();
            lcd.setCursor(0,0);
            lcd.print("Nissan Leaf S");
            lcd.setCursor(0,2);
            lcd.print("Miles: ");
            break;
          }
        }
      //Serial.println("00110");
      break;

    case 0:
      break;
  }

///////////////////////////////////////////////////////////////////////////////////////////////////
// These are the coordiantes for the joysticks and depending the coordinates decides the input for the controller,
  yPosition_1 = analogRead(A0);
  xPosition_2 = analogRead(A1);

  if ((yPosition_1 > 500) && (yPosition_1 < 520)) {
    //No movement
    SentMessage[0] = 000;
    radio.write(SentMessage, 1);
  } 

  if (yPosition_1 < 100) {
    //Backwards
    SentMessage[0] = 001;
    radio.write(SentMessage, 1);
  }

  if ((yPosition_1 < 500) && (yPosition_1 > 100)) {
    //Slower backwards
    SentMessage[0] = 010;
    radio.write(SentMessage, 1);
  }

  if (yPosition_1 > 1000) {
    //Forward
    SentMessage[0] = 100;
    radio.write(SentMessage, 1);
  }

  if ((yPosition_1 > 520) && (yPosition_1 < 1000)) {
    //Slower Forwards
    SentMessage[0] = 011;
    radio.write(SentMessage, 1);
  }

  if (xPosition_2 > 750) {
    //Turn Right
    SentMessage[0] = 110;
    radio.write(SentMessage, 1);
  }

  if (xPosition_2 < 250) {
    //Turn Left
    SentMessage[0] = 101;
    radio.write(SentMessage, 1);
  }

  timer = timer + 1;  //Global timer for how many cycles the code goes through
  
}

/////////////////////////////////////////////////////////////////////////////////////////////////

float switch_to_receiver(const byte vehicle[6]) {

//This fuction is used to switch the transmitter from transmitting to receiving to optain the battery percentage and
//display it on the LCD
  
  SentMessage[0] = 111;
  char battery[8] = "";
  long int kill_switch = 0;
  float lcd_battery;
  
  radio.write(SentMessage, 1);

  radio.begin();
  radio.openReadingPipe(0, vehicle);
  radio.startListening();

  while (!radio.available()) {
    kill_switch = kill_switch+1;
    //Serial.println("ERROR");
    radio.read(&battery, sizeof(battery));
    if (kill_switch > 10) {
      break;
    }
  }

  radio.read(&battery, sizeof(battery));

  radio.begin();
  radio.openWritingPipe(vehicle);
  radio.stopListening();

  Serial.println(atof(battery));
  lcd_battery = atof(battery);

  lcd.setCursor(0,3);
  lcd.print("Actual Battery:");

  lcd_battery = lcd_battery - .671;

  lcd.setCursor(14,3);
  lcd.print(battery);
  lcd.print(" ");
  return atof(battery);

}

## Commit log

2022-04-27 Update Schematic
    Fixed a mistake in Schematic
    [Car_Circuit.kicad_sch]
2022-04-27 Update Schematic
    Update Car Schematic Issue
